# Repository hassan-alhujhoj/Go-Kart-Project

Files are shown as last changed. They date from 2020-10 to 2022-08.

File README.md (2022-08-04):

# Go Kart Project

## Description
This project aims to design a control circuit that controls a current signal coming from Go-Kart circuitry.The controller board controls a Driver Board that is then interfaced a Power Circuitry Board that then powers a 3kW DC motor. The control board is based on the design of a fixed frequency current mode controller UC3843. This conroller board works by comparing throttle current (Idemand) with the motor current (Imeasured) that is read a current sensor (LEM HAIS 150P).

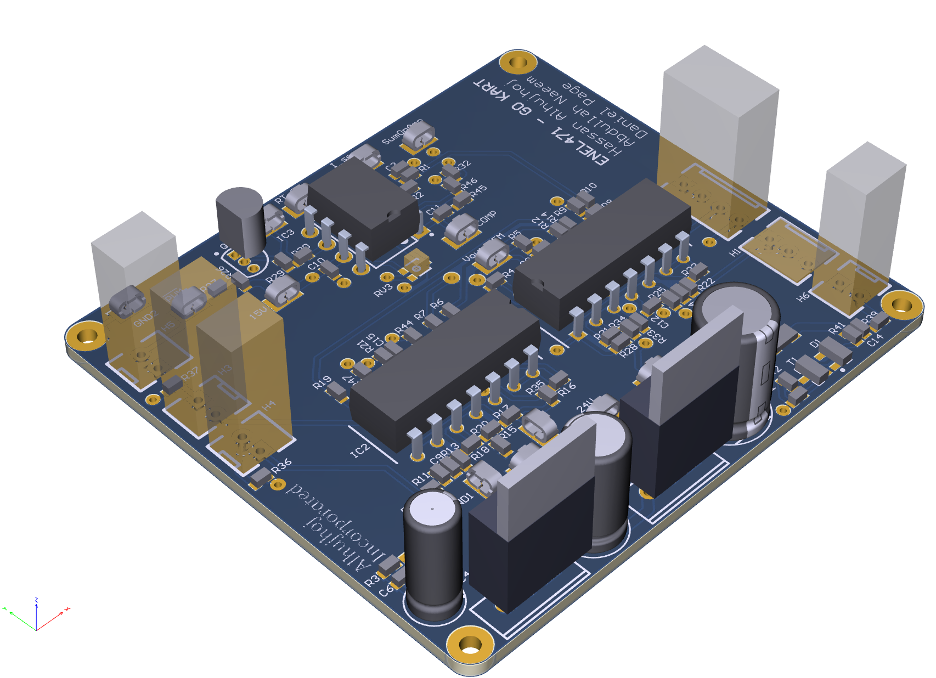
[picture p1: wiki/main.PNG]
Design
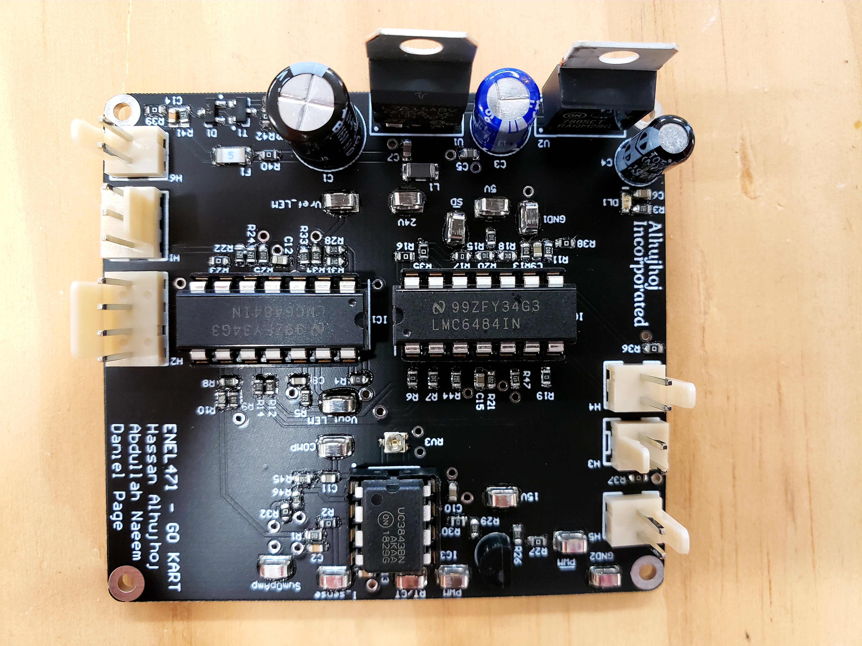
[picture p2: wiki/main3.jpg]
PCB
 Video

## Requirements
###  Design Constraints (essential for real life limitation for Go Kart electrical vehicles)
- Forwad motor current must not exceed 350A. The current-time area above 150A msut not be exceed for more than 100 Amp-seconds.
- Reverse motor current must not exeed 100A.
- Average forward motor currrent must not exceedd 150A.
- No MOSFET can be switched faster than 5kHz.
### Note: Violation of Deisgn Constraints will result in a 5-second shutdown.

## Important
- The PWM signal which the deiver uses to switch the MOSFETS.
- The shutdown control SD, which disables the MOSFET diver chip.
- The 24V DC supply from which all pwer supplies must be derived.
- The current sensor header connections.

## Goals
### Successfully Producing a PWM using UC3843 chip
* Voltage swing of 5V (referenced to GND).
* Rise and fall times < 1us.
* A PWM switching frequency of 2.5kHz+-10%.

### A PWM that is controllable via throttle
A normally open position switch has been installed on the brake pedal so that you can detect whenever the brake is operated. 
Your control system must be able to detect when the brake pedal has been depressed and immediately disable the drive circuitry. 
Reset this function by releasing the brake. When the Emergency Trip pushbutton switch is pressed it should disconnect all power 
to the motor and drive circuitry. When the switch is reset it should automatically re-enable the drive circuitry and put the 
cart in a safe ready-to-drive state. To earn full marks in this section your motor should not rotate when the throttle is not depressed.

### Implementation of a fixed current mode control
This requires you to sensibly use current feedback provided to you by the LEM sensor in your controller design. Your controller 
should be stable - your PWM should stay reasonably constant for a fixed throttle position and a fixed load. There should be no 
significant oscillations in any of the control signals.

### Throttle average current
Throttle sets average current and you limit aveage forward current to <150A, peak forward current to <350A and reverse current 
to <100A. Note: that you will only get full marks for this requirement if your controller actually attempts to push the average 
forward current >100A.

## Contributers
- [Hassan Alhujhoj](https://github.com/hassan-alhujhoj)
- [Abdullah Naeem](https://github.com/ana104-collab)
- [Daniel Page](https://github.com/Daniel-Page)

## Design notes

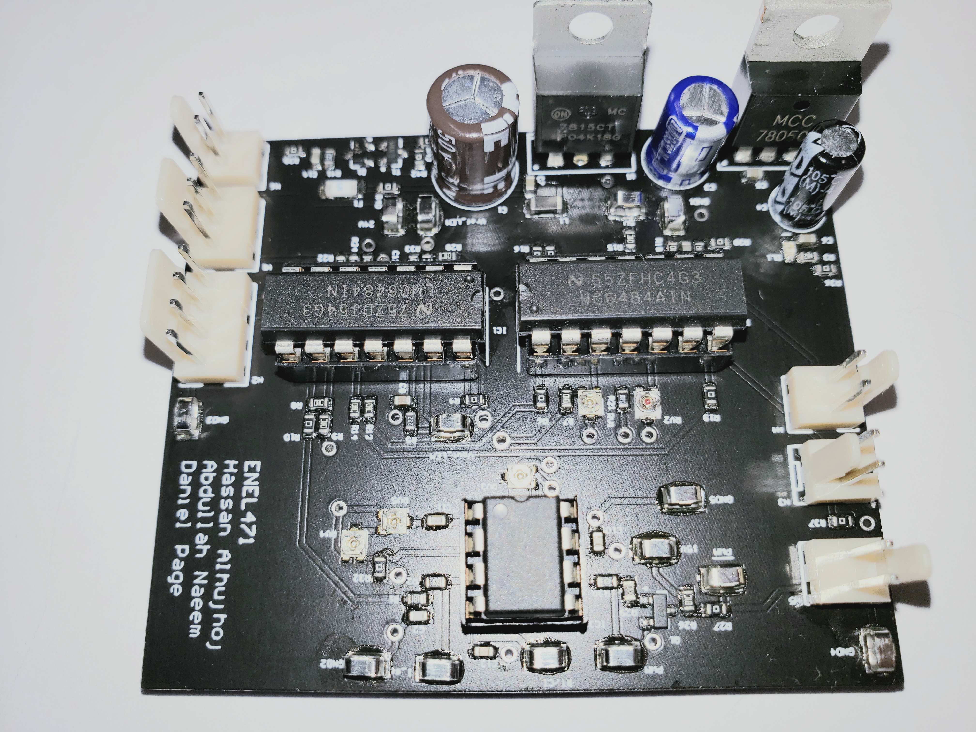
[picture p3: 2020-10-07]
wiki/main2.png

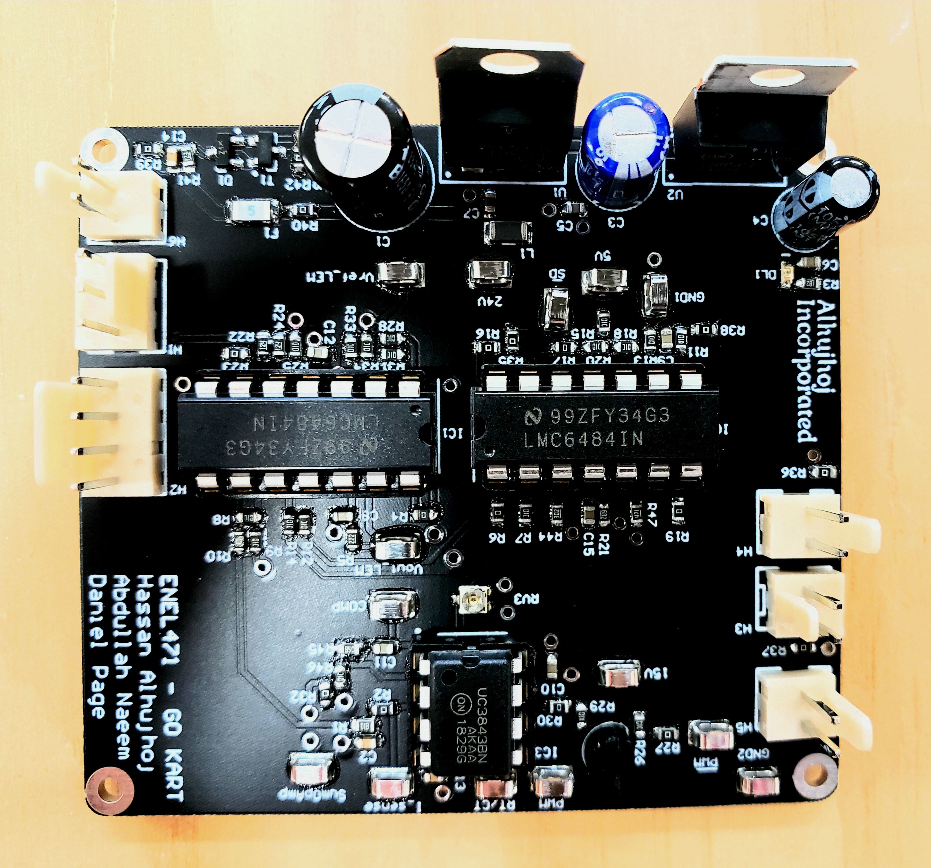
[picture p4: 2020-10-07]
wiki/main4.jpg

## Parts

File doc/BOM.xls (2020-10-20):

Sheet: BOM Report
Bill of Materials |  |  | Bill of Materials for PCB Document [GO_KART_CONTROLLER.PcbDoc]
Source Data From: |  | GO_KART_CONTROLLER.PcbDoc
Project: |  | GO_KART_Project.PrjPcb
Variant: |  | None
Creation Date: | 20/10/2020 | 11:28 PM
Print Date: | 2020-10-20 | 23:30:06
Footprint | Comment | LibRef | Designator | Description | Quantity
FP-ESLGM-MFG | 100uF | CMP-03015-000005-1 | C1 | CAP ALUM 100UF 20% 50V THRU HOLE. Part Number: ESL107M050AGMAA. Dia: 8mm. | 1
CAPC1608L | 6.8nF | CC_6.8nF_0603 | C2 | CAP CER 6.8nF X7R +-10% 50V 0603 | 1
FP-ESLE3-MFG | 47uF | CMP-03015-000004-1 | C3 | CAP ALUM 10UF 20% 100V THRU HOLE. Part Number: ESL106M100AE3AA. Dia: 6.3mm. | 1
FP-UPW1E220MDD-MFG | 1uF | CMP-12462-000010-1 | C4 | CAP ALUM 22UF 20% 25V RADIAL. Part Number: UPW1E220MDD. Dia: 5mm. | 1
CAPC1608L | 100nF | CC_100nF_0603 | C5, C6, C7, C9, C10, C12, C15 | CAP CER 100nF X7R +-10% 50V 0603 | 7
CAPC1608L | 1uF | CC_1uF_0603 | C8 | CAP CER 1uF Y5V -20% +80% 16V 0603 | 1
CAPC1608L | 2.2uF | CC_2.2uF_0603 | C11 | CAP CER 2.2uF X5R +-20% 10V 0603 | 1
CAPC1608L | 22nF | CC_22nF_0603 | C13 | CAP CER 22nF X7R +-10% 50V 0603 | 1
CAPC1608L | 15nF | CC_15nF_0603 | C14 | CAP CER 15nF X7R +-10% 50V 0603 | 1
SOT23_L | 4V7 | DZ_4.7V | D1 | BZX84C4V7LT1G - DIODE, ZENER, 4.7V, 225MW, SOT23 | 1
WL-SMCW0603 | Bright Green | DL_150060VS75000 | DL1 | LED Bright Green 40mcd 0603 SMD | 1
RESC3216N | 5A | FS_Fuse_5.0A | F1 | Fuse 5.0A Fast Acting 1206 SMD | 1
MOLEX_KK_3_HDR | 3 Pin Molex KK Hdr | JA_MOLEX_KK_3POS | H1 | CONN HEADER 3POS 2.54mm VERT_Thru Hole | 1
MOLEX_KK_4_HDR | 4 Pin Molex KK Hdr | JA_MOLEX_KK_4POS | H2 | CONN HEADER 4POS 2.54mm VERT_Thru Hole | 1
MOLEX_KK_2_HDR | 2 Pin Molex KK HDR | JA_MOLEX_KK_2POS | H3, H4, H5, H6 | CONN HEADER 2POS 2.54mm VERT_Thru Hole | 4
DIP794W56P254L1905H533Q14N | LMC6484IN | LMC6484IN | IC1, IC2 | Integrated Circuit | 2
DIP794W56P254L959H533Q8B | UC3843BNG | UC3843BNG | IC3 | Integrated Circuit | 1
INDC3216L | 1A max, Idc 0.3R, | IN_Ferrite-Bead | L1 | Ferrite Bead, Rdc 0.3R, Z100MHZ 600R, Imax 1A, SMD 1206 | 1
ONSC-TO-92-3-29-11 | 2N7000G | CMP-1058-00937-1 | Q1 | Small Signal MOSFET, 200 mA, 60 V, N-Channel, 3-Pin TO-92, Pb-Free, Bulk Box | 1
RESC1608L | 1K | RS_1K | R1 | RES 1.0K OHM 1/10W 5% 0603 SMD | 1
RESC1608L | 0R | RS_0R0 | R2, R4, R6, R10, R16, R17, R19, R23, R27, R30, R32, R35, R36, R37, R38, R39, R40, R42, R43 | RES 0.0 OHM 1/10W 5% 0603 SMD | 19
RESC1608L | 1K8 | RS_1K8 | R3 | RES 1.8K OHM 1/10W 5% 0603 SMD | 1
RESC1608L | 2K2 | RS_2K2 | R5 | RES 2.2K OHM 1/10W 5% 0603 SMD | 1
RESC1608L | 10K | RS_10K | R7, R8, R9, R12, R14, R15, R18, R20, R26, R28, R31, R33, R34, R46 | RES 10.0K OHM 1/10W 5% 0603 SMD | 14
RESC1608L | 100R | RS_100R | R11 | RES 100 OHM 1/10W 5% 0603 SMD | 1
RESC1608L | 100K | RS_100K | R13, R25 | RES 100K OHM 1/10W 5% 0603 SMD | 2
RESC1608L | 6K8 | RS_6K8 | R21 | RES 6k8 OHM 1/10W 5% 0603 SMD | 1
RESC1608L | 120K | RS_120K | R22, R24 | RES 120K OHM 1/10W 5% 0603 SMD | 2
RESC1608L | 10R | RS_10R | R29 | RES 10 OHM 1/10W 5% 0603 SMD | 1
RESC1608L | 12K | RS_12K | R41 | RES 12K OHM 1/10W 5% 0603 SMD | 1
RESC1608L | 3K | RS_3K | R44 | RES 3K OHM 1/10W 5% 0603 SMD | 1
RESC1608L | 68K | RS_68K | R45 | RES 68.0K OHM 1/10W 5% 0603 SMD | 1
RESC1608L | 470R | RS_470R | R47 | RES 470 OHM 1/10W 5% 0603 SMD | 1
RESC1608L | 3K9 | RS_3K9 | R48 | RES 3.9K OHM 1/10W 5% 0603 SMD | 1
RESC1608L | 4K3 | RS_4K3 | R49 | RES 4.3K OHM 1/10W 5% 0603 SMD | 1
PVZ2A | 100K | RM_100K | RV3 | Trim Pot SMD 100K Murata PVZ2 Series SMD | 1
SOT23_L | BSH114,215 | TM_BSH114 | T1 | MOSFET N-CH 100V 0.85A SOT-23 | 1
TO220 | L7815CV | CMP-0244-00422-1 | U1 | Positive Voltage Regulator, 15V, 3-Pin TO-220 | 1
TO220 | L7805ACV | CMP-0244-00484-1 | U2 | Positive Voltage Regulator, 5V, 3-Pin TO-220 | 1
 |  |  |  |  | 82
Approved |  | Notes

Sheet: Project Information
Project Full Path | C:\Users\haa61\OneDrive - University of Canterbury\Desktop\Semester2_2020\ENEL471\Go Kart Assignment\GO_CART_PCB\gokartproject\GO_KART_Project.PrjPcb
Project Filename | GO_KART_Project.PrjPcb
Variant Name | None
Data-Source Filename | GO_KART_CONTROLLER.PcbDoc
Data-Source Full Path | C:\Users\haa61\OneDrive - University of Canterbury\Desktop\Semester2_2020\ENEL471\Go Kart Assignment\GO_CART_PCB\PCB_Project1\GO_KART_CONTROLLER.PcbDoc
Title | Bill of Materials for PCB Document [GO_KART_CONTROLLER.PcbDoc]
Total Quantity | 82
Report Time | 11:28 PM
Report Date | 20/10/2020
Report Date & Tine | 20/10/2020 11:28 PM
Output Name | Bill of Materials
Output Type | BOM_PartType
Output Generator Name | BOM
Output Generator Description | Bill of Materials

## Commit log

2020-09-15 Go Kart Altium design project.
    [Connectors&TestPoints.SchDoc, GO_CART_Project.PrjPcb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]
2020-09-15 Removed unnecassary files and folders
    [main-DESKTOP-L9L0IAD.SchDoc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]
2020-09-19 New updates to PCB
    [Connectors&TestPoints.SchDoc, GO_CART_Project.PrjPcb, GO_CART_Project.xlsx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]
2020-09-20 Renaming project files
    [GO_KART_Project.PrjPcb]
2020-09-20 Updated PCB Design and Added Final Touches
    [main.SchDoc]
2020-09-20 Added Round Edges to PCB
2020-09-21 Added Gerbel Files
    [GO_KART_Project.PrjPcb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]
2020-09-21 Added a wiki folder
    [GO_KART_Project.PrjPcb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]
2020-09-28 Updates to schematics
    [GO_KART_Project.PrjPcb, main.SchDoc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]
2020-09-28 Pulled the changes
    [GO_KART_Project.PrjPcb, main.SchDoc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]
2020-10-07 New updates
    [Connectors&TestPoints.SchDoc, GO_KART_Project-Hassan’s MacBook Pro (2).PrjPcb, GO_KART_Project.PrjPcb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]
2020-10-20 Added a bill of material and schematics
    [BOM.xls, Connectors&TestPoints.SchDoc, GO_KART_Project.PrjPcb]
2020-10-20 added a src and doc folder
    [BOM.xls, Connectors&TestPoints.SchDoc, GO_KART_Project.PrjPcb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]
